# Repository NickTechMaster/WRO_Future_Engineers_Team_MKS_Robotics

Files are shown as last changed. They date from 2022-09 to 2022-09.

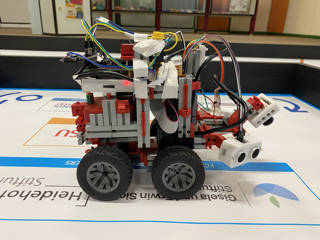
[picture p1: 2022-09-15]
Bilder & Videos/Bilder/Rechts.png

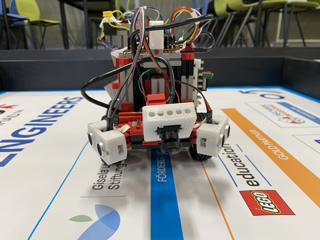
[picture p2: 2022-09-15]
Bilder & Videos/Bilder/Vorne.png

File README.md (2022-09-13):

<h1>Dokumentation WRO </h1>
<h3>Bei dem Vorentscheid haben wir einen Fischertechnik-TXT4.0-Roboter verwendetet. Da dieser fast keine Python Dokumentation besitzt, die Sensoren und Motoren extrem teuer und Fehleranfällig sind, haben wir uns für dieses Finale entschieden, auf einen Raspberry-Pi-Microcontroller umzusteigen. Unser momentanes Auto besteht trotzdem überwiegend aus Fischertechnik Steck-Teilen, da diese stabil und leicht veränderbar sind. Aber wir benutzen ganz andere technische Komponenten: Momentan haben wir 2 Ultraschallsensoren (links und rechts), ein Servomotor hinten platziert, da wir so besser um die Kurven fahren können, einen sogenannten „Fischertechnik-Hat“, mit welchem wir den Encomoter des Fischertechniksets steuern können, eine 170 Grad-Kamera, um die Hindernisse zu erkennen und um am Ende des Eröffnungsrennen stehen zu bleiben; und natürlich den Raspberry 3B mit einem „Aufsatz“ und einem Display. Diese ganzen Elemente sind mit Jumper-Kabel verbunden. Für die Ultraschallsensor haben wir noch eine Platine gelötet, da die Ultraschall Sensoren Wiederstände brauchen. Diese Verbesserungen ermöglichten uns viele Vorteile. Einerseits sind wir viel freier bei den Komponenten des Roboters. Zum Beispiel kostet ein Sensor von Raspberry oder Arduino maximal 10€, wo hingegen ein Sensor von Fischertechnik bei 50€ anfängt. Wir haben auch viel mehr Vorteile dadurch, weil wir uns die Gehäuse und Halterungen dieser Sensoren einfach in einem 3D-Drucker drucken konnten. Dafür mussten wir die ganzen Gehäuse und Befestigungen modellieren. Darüber hinaus konnten wir den Roboter in seiner software so anpassen wie wir es wollten. Wir haben unser Programm in der Programmiersprache python geschrieben. Diese Skripte haben wir dann über ein lokales Netzwerk zwischen dem Rasberry pi und dem Computer hochgeladen. In dem Programm nimmt sich der Roboter bei dem Eröffnungsrennen die Werte von den Ultraschallsensoren, welche links und rechts am Roboter leicht schräg positioniert sind. Aus diesen Werten rechnet der Roboter den Mittelpunkt aus und versucht sich die ganze Zeit sich diesem zu nähern. Dabei lenkt er umso mehr er vom Mittelpunkt entfernt ist. Zum Stoppen am Ende des Rennens benutzen wir eine Kamera, welche die blauen Linien zählt und nach 12 erfassten Linien nach ca. 3-5 Sekunden stehen bleibt. Diese sogenannte Kamera ist eine 170 Grad Kamera und wir benutzen sie auch bei dem Hindernisrennen. Hier benutzen wir zum Fahren das Programm von dem Eröffnungsrennen und fügen zum Beispiel hinzu, dass wenn die Kamera grün erkennt sich der Mittelpunkt nach links verschiebt und wir so keine Strecken „hard coden“ müssen und das Auto weiterhin autonom fährt. Das gleiche passiert bei Rot nur der Mittelpunkt wird nach rechts verschoben wird.</h3>

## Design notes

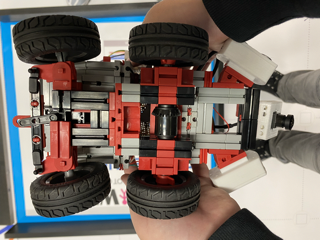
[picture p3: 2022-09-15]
Bilder & Videos/Bilder/Unten.png

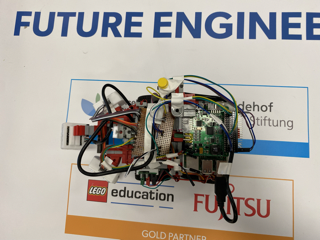
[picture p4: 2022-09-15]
Bilder & Videos/Bilder/Oben.png

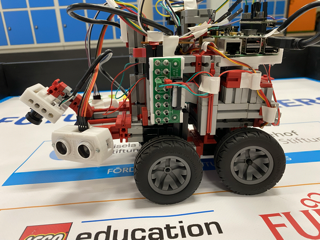
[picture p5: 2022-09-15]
Bilder & Videos/Bilder/Links.png

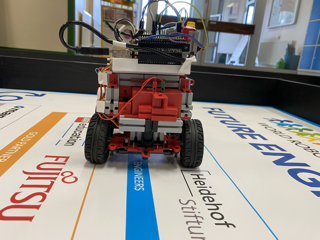
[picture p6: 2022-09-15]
Bilder & Videos/Bilder/Hinten.png

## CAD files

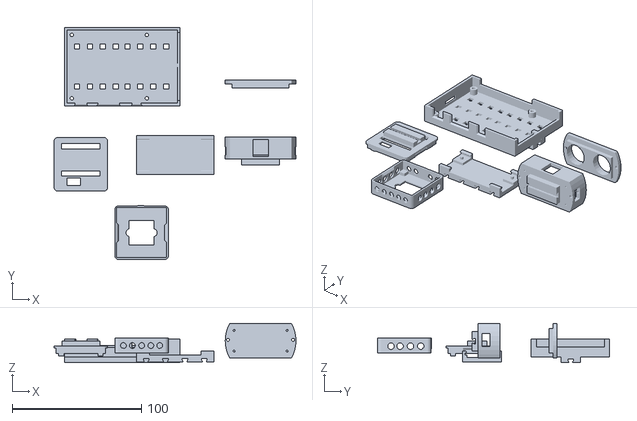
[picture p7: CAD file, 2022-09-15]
Zeichnungen & 3D Druck/3D Druck/3D_Druck.stl
187.1 x 179.5 x 30.4

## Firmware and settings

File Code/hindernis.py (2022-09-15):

#Bibiliotheken importieren
import RPi.GPIO as GPIO
import time
import cv2
import numpy as np
from gpiozero import Button


#GPIO Pins festlegen
GPIO.setmode(GPIO.BCM)
GPIO.setwarnings(False)


GPIO.setup(26, GPIO.OUT)
servo = GPIO.PWM(26, 50)


GPIO.setup(19, GPIO.OUT)
GPIO.output(19, GPIO.HIGH)

GPIO.setup(13, GPIO.OUT)
pwm = GPIO.PWM(13, 50)
pwm.start(0)
GPIO.output(13, GPIO.HIGH)


GPIO.setup(5, GPIO.OUT)

GPIO.setup(6, GPIO.OUT)


GPIO.setup(21, GPIO.OUT)
GPIO.setup(20, GPIO.IN)

GPIO.setup(16, GPIO.OUT)
GPIO.setup(12, GPIO.IN)

GPIO.setup(1, GPIO.OUT)
GPIO.setup(0, GPIO.IN)


lower_green = np.array([42, 30, 20])
upper_green = np.array([68, 250, 255])

lower_red = np.array([1, 70, 20])
upper_red = np.array([6, 190, 255])


vid = cv2.VideoCapture(0) 

time.sleep(4)


#Ultraschall Sensoren ansteuern
def ultraschall(mode):

    if mode == 0:
        GPIO_TRIGGER = 21
        GPIO_ECHO = 20
    elif mode == 1:
        GPIO_TRIGGER = 16
        GPIO_ECHO = 12
    else:
        GPIO_TRIGGER = 1
        GPIO_ECHO = 0
    distanz_all = 0

    GPIO.output(GPIO_TRIGGER, True)

    time.sleep(0.00001)
    GPIO.output(GPIO_TRIGGER, False)

    StartZeit = time.time()
    StopZeit = time.time()

    while GPIO.input(GPIO_ECHO) == 0:
        StartZeit = time.time()

    while GPIO.input(GPIO_ECHO) == 1:
        StopZeit = time.time()


    TimeElapsed = StopZeit - StartZeit
    distanz = (TimeElapsed * 34300) / 2

    return(round(distanz))


#Motor ansteuern
def motor(mode, speed):
    if mode == "stop":
        pins = { 19:GPIO.HIGH, 5:GPIO.HIGH, 6:GPIO.HIGH, 13:GPIO.HIGH }
        for p in list(pins.keys()):
            GPIO.output(p, pins[p])

    elif mode == "forward":
        pins = { 19:GPIO.HIGH, 5:GPIO.HIGH, 6:GPIO.LOW, 13:GPIO.HIGH }
        for p in list(pins.keys()):
            GPIO.output(p, pins[p])
        pwm.ChangeDutyCycle(speed)

    elif mode == "backward":
        pwm.start(0)
        pins = { 19:GPIO.HIGH, 5:GPIO.LOW, 6:GPIO.HIGH, 13:GPIO.HIGH }
        for p in list(pins.keys()):
            GPIO.output(p, pins[p])
        pwm.ChangeDutyCycle(speed)

direction = ""

while True:
    motor("forward", 100)

    #Ultraschall Sensoren definieren
    rechts = ultraschall(0) 

    links = ultraschall(2)


    if links < 450 and rechts < 450:


        ret, frame = vid.read()


        area = 0
        area_green = 0
        area_red = 0

        
        #bild aufnehmen und häller machen
        Intensity_Matrix=np.ones(frame.shape, dtype = "uint8") * 0

        frame = cv2.add(frame, Intensity_Matrix)
        
        
        height, width = frame.shape[:2]
        area_frame = height * width

        lowest_green = height + 1
        lowest_red = height + 1

        image = cv2.cvtColor(frame, cv2.COLOR_BGR2HSV)
        
        #erkennen ob grün oder rot erkannt wird
        mask_green = cv2.inRange (image, lower_green, upper_green)
        contours_green, hierarchy = cv2.findContours(mask_green, cv2.RETR_EXTERNAL, cv2.CHAIN_APPROX_SIMPLE)

        mask_red = cv2.inRange (image, lower_red, upper_red)
        contours_red, hierarchy = cv2.findContours(mask_red, cv2.RETR_EXTERNAL, cv2.CHAIN_APPROX_SIMPLE)

        if len(contours_green) != 0:
            for contour in contours_green:
                if cv2.contourArea(contour) > 500:
                    print("color_green_detected")
                    x, y, w, h = cv2.boundingRect(contour)

                    cv2.rectangle(frame, (x,y), (x + w, y + h), (0, 255, 0), 3)
                    area = h * w
                    area_green = area_green + area 
                    if y < lowest_green:
                        lowest_green = y

        if len(contours_red) != 0:
            for contour in contours_red:
                if cv2.contourArea(contour) > 500:
                    print("color_red_detected")
                    x, y, w, h = cv2.boundingRect(contour)
                    cv2.rectangle(frame, (x,y), (x + w, y + h), (0, 0, 255), 2)
                    area = h * w
                    area_red = area_red + area 
                    if y < lowest_red:
                        lowest_red = y
        ready = True


        if round(100 * area_green / area_frame) > 12 and round(100 * area_red / area_frame) > 12:
            if lowest_green > lowest_red:
                print("control green p")

            elif lowest_red > lowest_green:
                print("control red p")
  
        elif round(100 * area_green / area_frame) > 1:
            print("control green")
            rechts = rechts + 72
        elif round(100 * area_red / area_frame) > 10:
            print("control red")
            direction = "innen"
 
        else:
            control = False
            direction = ""


        #lenkung ausrechenen und ausweichmanöver einleiten

        mittelpunkt = (links + rechts) / 2


        if direction == "außen":
            rechts = rechts * 2.6 + 29
        elif direction == "innen":
            links = links * 2.4 + 30


        #links
        if links <= rechts:
            lenkung = round(100 - (100 * links / mittelpunkt))
            servo.start(7 - lenkung * 0.025)


        #rechts

        elif rechts <= links:

            lenkung = round(100 - (100 * rechts / mittelpunkt))
            servo.start(7 + lenkung * 0.025)


    #motor stoppen wenn programm manuel beendet wird
    try:
        pass
    except KeyboardInterrupt:
        pins = { 19:GPIO.HIGH, 5:GPIO.HIGH, 6:GPIO.HIGH, 13:GPIO.HIGH }
        for p in list(pins.keys()):
            GPIO.output(p, pins[p])
